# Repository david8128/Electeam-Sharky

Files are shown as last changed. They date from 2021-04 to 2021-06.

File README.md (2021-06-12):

# Electeam-Sharky-ESP32

## OrderMe:
1N4728A: caída de voltaje de 3 a 3.5V - CONFIRMAR
## ORDERED:
This is the firmware for the ESP32-DEVKITV1 microcontroller where throttle, break, LCD screen, motor and more systems are integrated.

Schematic 
<!-- TODO Update schematic here -->
> The PCB Kicad folder is located in (controller_bldc_kicad_Sch_PCB/)[https://github.com/david8128/Electeam-Sharky-ESP32/tree/main/controller_bldc_kicad_Sch_PCB]
## Electrical Specifications for the PCB electronics
<!-- Note the reference of nextion in README, 70mA -->
<!-- TODO Document the current and voltage in Current Sensor -->

<!-- TODO Add the MCU and SMPS specs in README-->
#### Power 
Relay for the Operator Presence Control - aka. Death Man Security System (HAT901 12VDC 20A) = 0.96 W
>MOSFET has been considered for de OPC but the consumtion is higher (Using IRF1010N with a )
For this project is used the MCPWM BLDC motor control (hall sensor feedback) example from ESP-IDF library.

As shown in Schematic there were used two [LM2596 DC-DC HW-411](http://tpelectronic.ir/datasheets/20150123144301750.pdf) converters 

#### Battery
When battery is fully charged the voltage is 40.6V. The BMS open the discharging circuit when the battery voltage is under 32V. 

The energy or maximum energetic storage capacity of the battery is 320Wh.

*This modes will be reviewed under the light of the Shell Echo Marathon Competition.*
## Modes

### Acceleration Optimized

### Soft Start

### Manual

Here you have the documentation of the MCPWM-Hall_Sensor example:

## MCPWM BLDC motor control(hall sensor feedback) Example

This example will show you how to use MCPWM module to control bldc motor with hall sensor feedback
 
The following examples uses MCPWM module to control bldc motor and vary its speed continuously

The bldc motor used for testing this code had hall sensor capture sequence of 6-->4-->5-->1-->3-->2-->6-->4--> and so on

IR2103 3-ph bridge driver is used for testing this example code

User needs to make changes according to the motor and gate driver ic used

## Step 1: Pin assignment
* The gpio init function initializes:
	* GPIO19 is assigned as the MCPWM signal for 1H(UH)
	* GPIO18 is assigned as the MCPWM signal for 1L(UL)
	* GPIO17 is assigned as the MCPWM signal for 2H(VH)
	* GPIO16 is assigned as the MCPWM signal for 2L(VL)
	* GPIO15 is assigned as the MCPWM signal for 3H(WH)
	* GPIO14 is assigned as the MCPWM signal for 3L(WL)
	* GPIO23 is assigned as the MCPWM capture signal for Hall A
	* GPIO25 is assigned as the MCPWM capture signal for HALL B
	* GPIO26 is assigned as the MCPWM capture signal for HALL C

## Step 2: Initialize MCPWM
 * You need to set the frequency and duty cycle of MCPWM timer
 * You need to set the MCPWM channel you want to use, and bind the channel with one of the timers
 * You need to set the capture unit, for POS/NEG edge capture
 * Also reversing the hall sensor BIT weight, will make bldc motor rotate CW or CCW

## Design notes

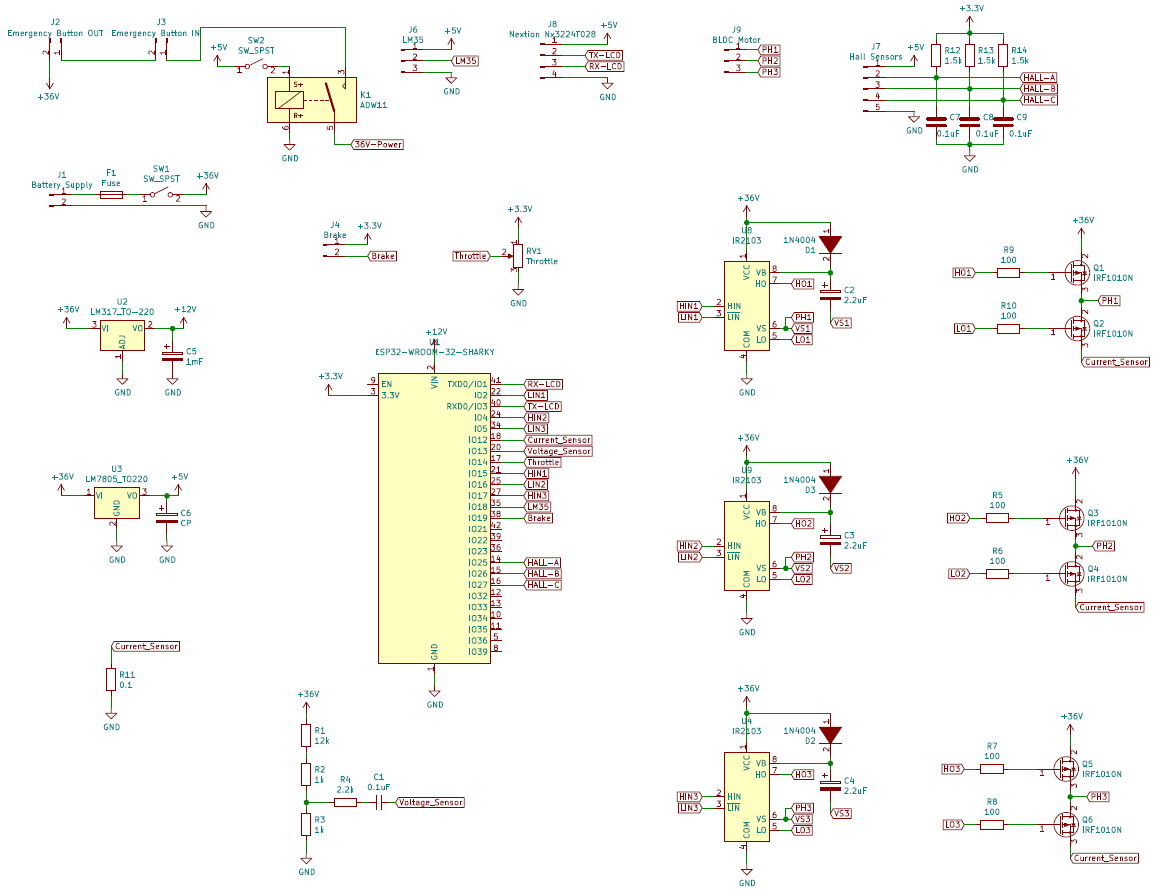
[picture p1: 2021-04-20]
Diseño Electrónico/Esquema y Gerbers PCB/Schematic.png

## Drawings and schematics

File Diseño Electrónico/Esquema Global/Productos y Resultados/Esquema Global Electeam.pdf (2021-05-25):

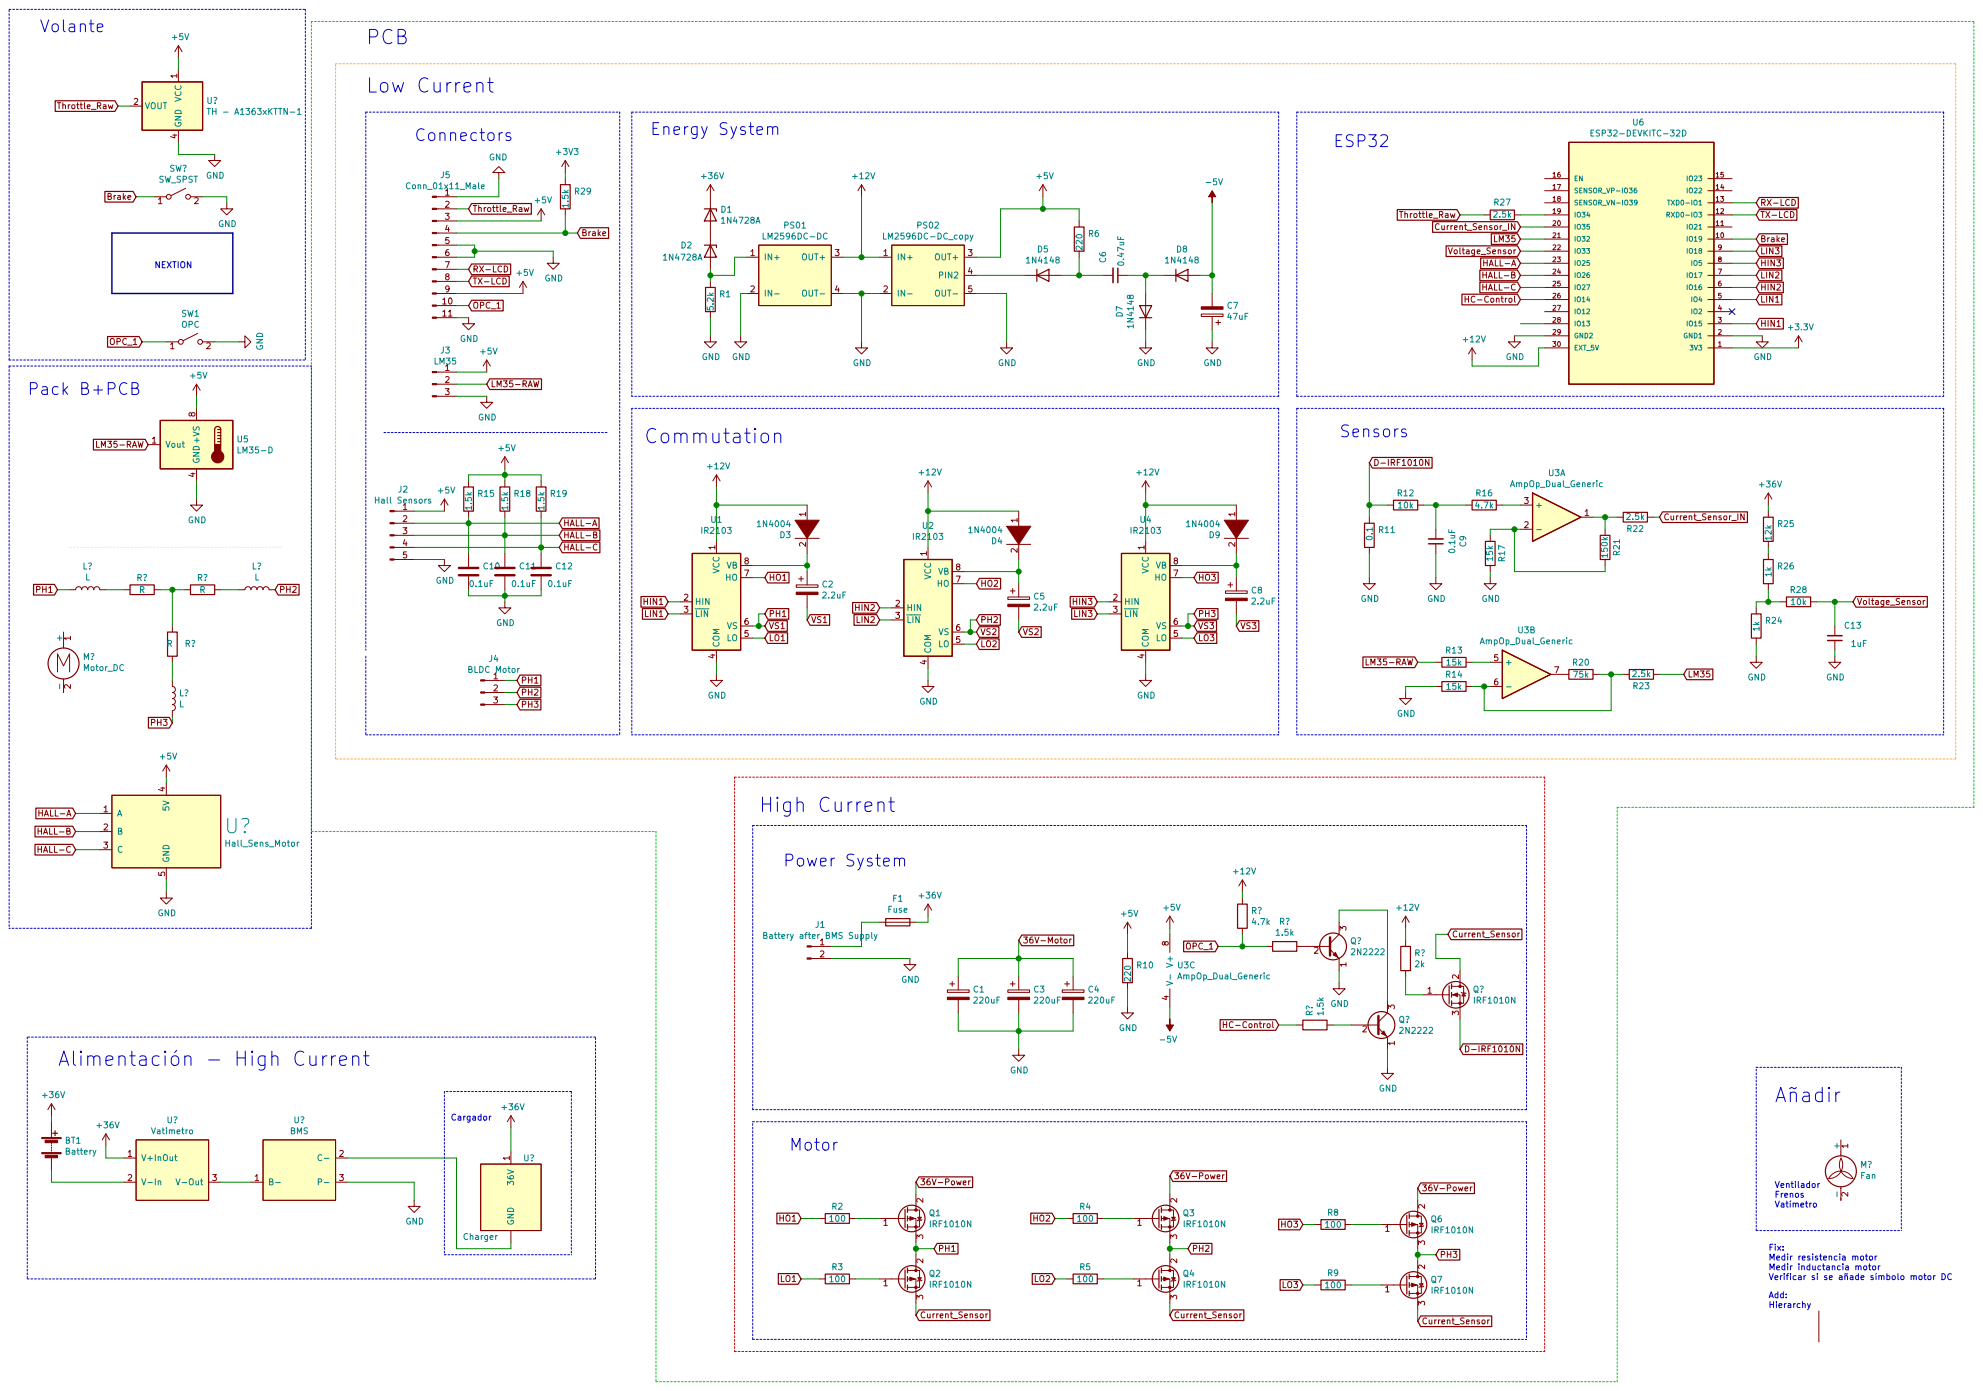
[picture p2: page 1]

Fix: Medir resistencia motor Medir inductancia motor Verificar si se añade símbolo motor DC Commutation

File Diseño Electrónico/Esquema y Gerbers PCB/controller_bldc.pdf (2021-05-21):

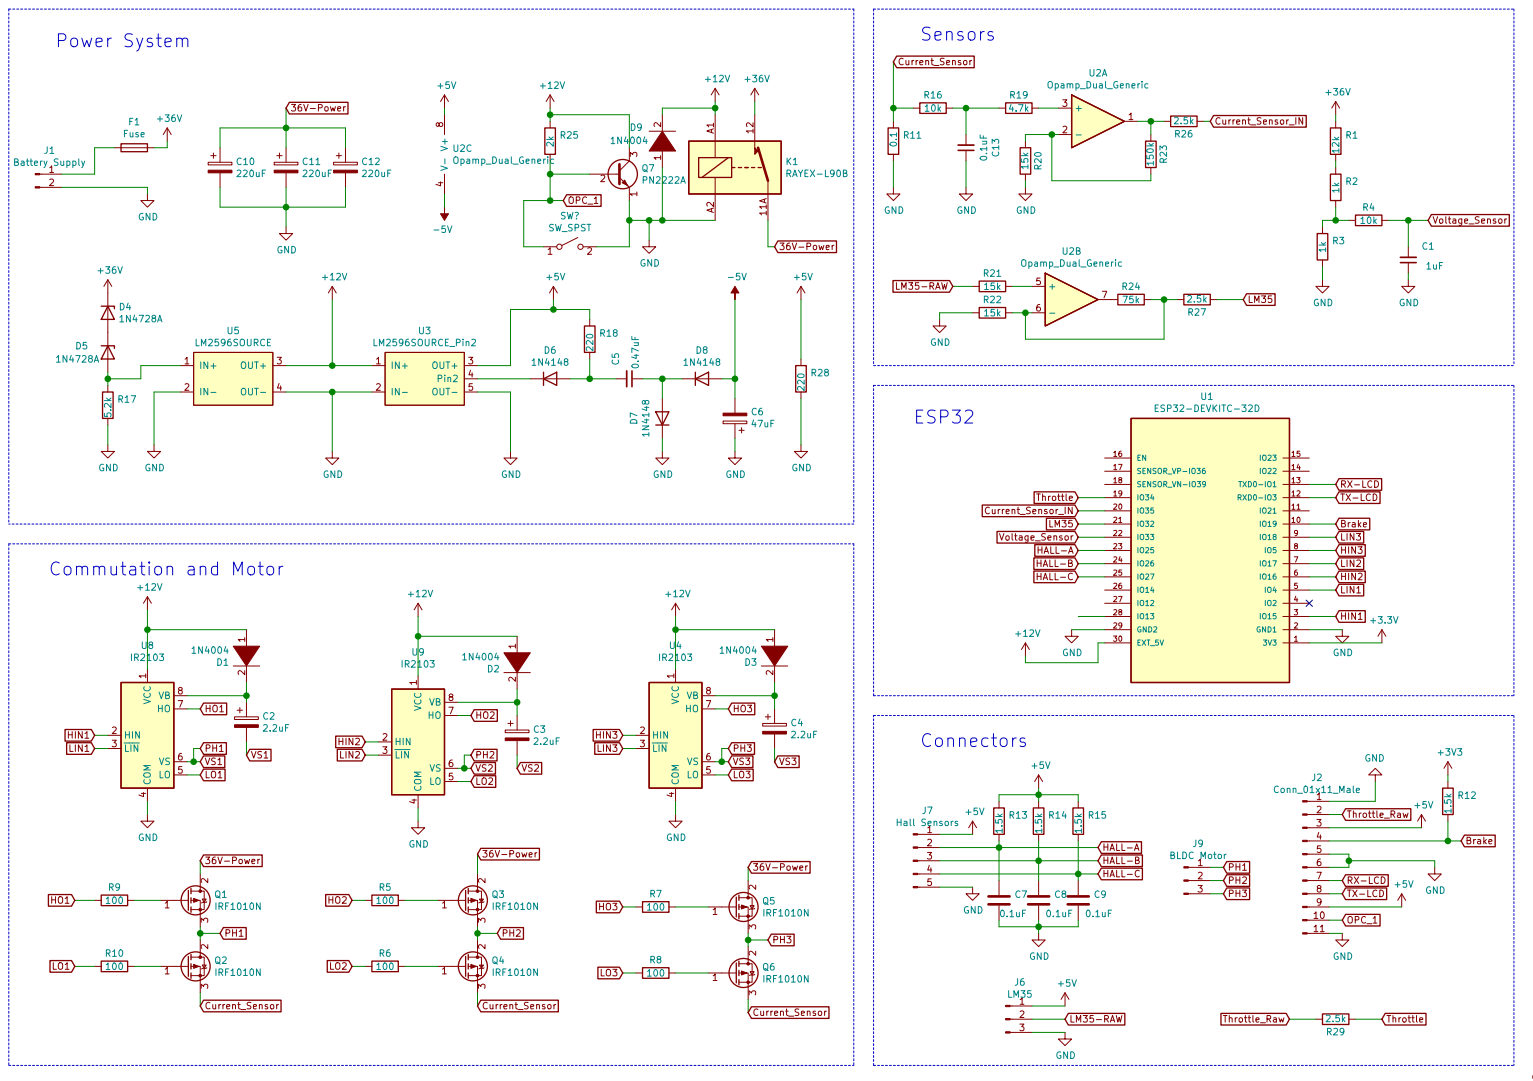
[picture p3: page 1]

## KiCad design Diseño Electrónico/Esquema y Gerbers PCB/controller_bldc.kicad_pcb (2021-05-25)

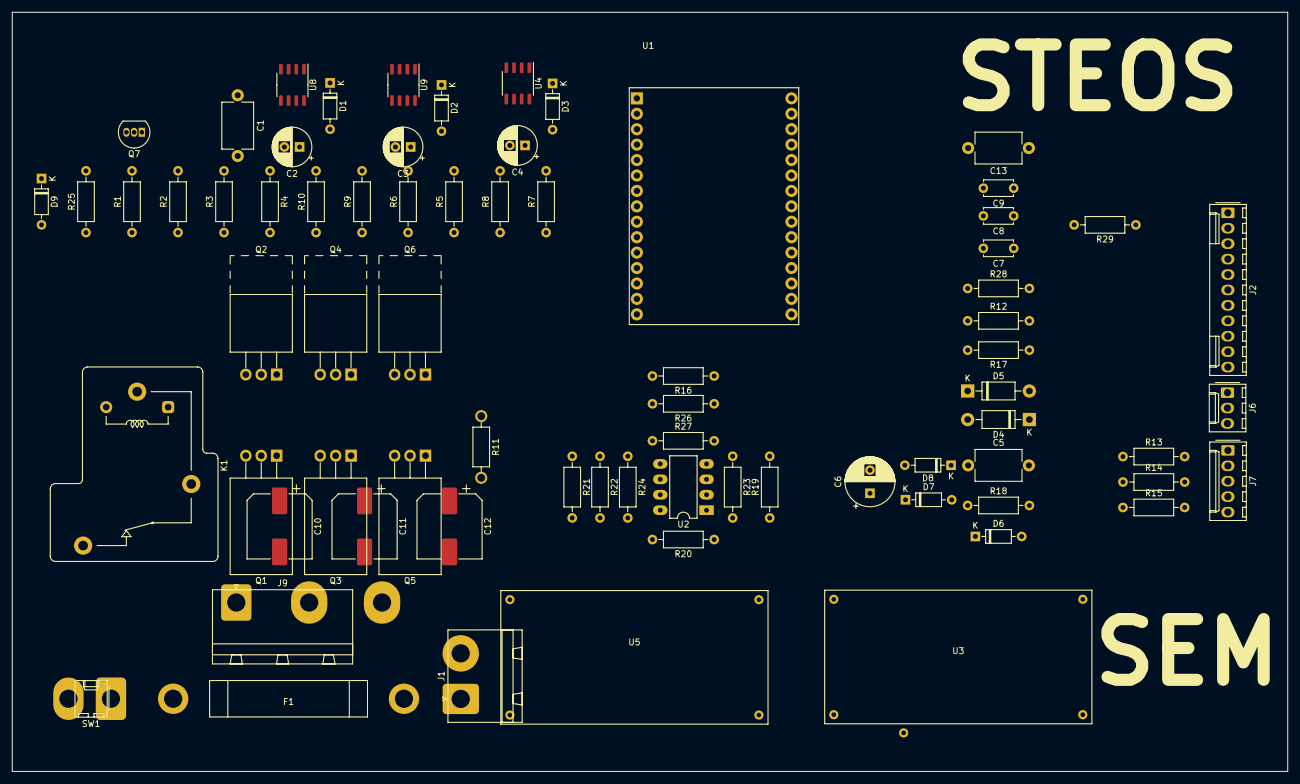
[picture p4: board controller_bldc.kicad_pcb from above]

Board: 2 copper layers, 210.0 x 125.0 mm, 73 parts (0 on the bottom side), 61 nets, no tracks yet.

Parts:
C1: 1uF; C_Disc_D7.5mm_W5.0mm_P10.00mm
C2, C3, C4: 2.2uF; CP_Radial_D6.3mm_P2.50mm
C5: 0.47uF; C_Disc_D7.5mm_W5.0mm_P10.00mm
C6: 47uF; CP_Radial_D8.0mm_P3.80mm
C7, C8, C9: 0.1uF; C_Disc_D4.7mm_W2.5mm_P5.00mm
C10, C11, C12: 220uF; CP_Elec_10x14.3
C13: 0.1uF; C_Disc_D7.5mm_W5.0mm_P10.00mm
D1, D2, D3, D9: 1N4004; D_DO-35_SOD27_P7.62mm_Horizontal
D4, D5: 1N4728A; D_DO-41_SOD81_P10.16mm_Horizontal
D6, D7, D8: 1N4148; D_DO-35_SOD27_P7.62mm_Horizontal
F1: Fuse; Portafusible
J1: Battery Supply; PhoenixContact_GMSTBA_2,5_2-G_1x02_P7.50mm_Horizontal
J2: Conn_01x11_Male; Molex_KK-254_AE-6410-11A_1x11_P2.54mm_Vertical
J6: LM35; Molex_KK-254_AE-6410-03A_1x03_P2.54mm_Vertical
J7: Hall Sensors; Molex_KK-254_AE-6410-05A_1x05_P2.54mm_Vertical
J9: BLDC Motor; PhoenixContact_GMSTBA_2,5_3-G-7,62_1x03_P7.62mm_Horizontal
K1: RAYEX-L90B; Relay_SPST_RAYEX-L90B
Q1, Q3, Q5: IRF1010N; TO-220-3_Horizontal_TabDown
Q2, Q4, Q6: IRF1010N; TO-220-3_Horizontal_TabUp
Q7: PN2222A; TO-92_Inline
R1: 12k; R_Axial_DIN0207_L6.3mm_D2.5mm_P10.16mm_Horizontal
R2, R3: 1k; R_Axial_DIN0207_L6.3mm_D2.5mm_P10.16mm_Horizontal
R4, R16: 10k; R_Axial_DIN0207_L6.3mm_D2.5mm_P10.16mm_Horizontal
R5, R6, R7, R8, R9, R10: 100; R_Axial_DIN0207_L6.3mm_D2.5mm_P10.16mm_Horizontal
R11: 0.1; R_Axial_DIN0207_L6.3mm_D2.5mm_P10.16mm_Horizontal
R12, R13, R14, R15: 1.5k; R_Axial_DIN0207_L6.3mm_D2.5mm_P10.16mm_Horizontal
R17: 5.2k; R_Axial_DIN0207_L6.3mm_D2.5mm_P10.16mm_Horizontal
R18: 220; R_Axial_DIN0207_L6.3mm_D2.5mm_P10.16mm_Horizontal
R19: 4.7k; R_Axial_DIN0207_L6.3mm_D2.5mm_P10.16mm_Horizontal
R20, R21, R22: 15k; R_Axial_DIN0207_L6.3mm_D2.5mm_P10.16mm_Horizontal
R23: 150k; R_Axial_DIN0207_L6.3mm_D2.5mm_P10.16mm_Horizontal
R24: 75k; R_Axial_DIN0207_L6.3mm_D2.5mm_P10.16mm_Horizontal
R25: 2k; R_Axial_DIN0207_L6.3mm_D2.5mm_P10.16mm_Horizontal
R26, R27, R29: 2.5k; R_Axial_DIN0207_L6.3mm_D2.5mm_P10.16mm_Horizontal
R28: 1.2k; R_Axial_DIN0207_L6.3mm_D2.5mm_P10.16mm_Horizontal
SW1: ON_OFF; Molex_KK-254_AE-6410-02A_1x02_P2.54mm_Vertical
U1: ESP32-DEVKITC-32D; MODULE_ESP32-DEVKITC-32D
U2: MC1458P; DIP-8_W7.62mm_LongPads
U3: LM2596SOURCE_Pin2; LM2596DCSourcePin2_Electeam
U4, U8, U9: IR2103; SO-8_3.9x4.9mm_P1.27mm
U5: LM2596SOURCE; LM2596DCSource_Electeam

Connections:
1IN-: R20.1, R23.1, R26.1, U2.2
2IN-: R22.1, R24.1, R27.1, U2.6
36V-Power: C10.1, C11.1, C12.1, K1.11A, K1.11B, Q1.2, Q3.2, Q5.2
+3V3: R12.1, U1.1
+5V: J2.3, J2.9, J6.1, J7.1, R13.1, R14.1, R15.1, R18.1, U2.8, U3.3
+12V: D1.1, D2.1, D3.1, D9.2, K1.A1, Q7.3, R25.1, U1.30, U3.1, U4.1, U5.3, U8.1, U9.1
+36V: D4.1, K1.12, R1.1, SW1.2
-5V: C6.2, D8.2
Brake: J2.4, R12.2, U1.10
Current_Sensor: Q2.3, Q4.3, Q6.3, R11.1, R16.2
Current_Sensor_AO: C13.2, R16.1, R19.2
Current_Sensor_IN: R26.2, U1.19
GND: C1.1, C6.1, C7.2, C8.2, C9.2, C10.2, C11.2, C12.2, C13.1, D7.1, D9.1, J1.2, J2.1, J2.5, J2.6, J2.11, J6.3, J7.5, K1.A2, Q7.1, R3.2, R11.2, R17.2, R20.2, R22.2, R28.2, U1.2, U1.29, U2.4, U3.2, U3.5, U4.4, U5.2, U5.4, U8.4, U9.4
HALL-A: C7.1, J7.2, R13.2, U1.23
HALL-B: C8.1, J7.3, R14.2, U1.24
HALL-C: C9.1, J7.4, R15.2, U1.25
HIN1: U1.3, U8.2
HIN2: U1.6, U9.2
HIN3: U1.8, U4.2
HO1: R9.2, U8.7
HO2: R5.2, U9.7
HO3: R7.2, U4.7
LIN1: U1.5, U8.3
LIN2: U1.7, U9.3
LIN3: U1.9, U4.3
LM35: R27.2, U1.18
LM35-RAW: J6.2, R21.2
LO1: R10.2, U8.5
LO2: R6.2, U9.5
LO3: R8.2, U4.5
unnamed: C2.1, D1.2, U8.8
unnamed: C3.1, D2.2, U9.8
unnamed: C4.1, D3.2, U4.8
unnamed: C5.1, D7.2, D8.1
unnamed: C5.2, D6.2, R18.2
unnamed: D4.2, D5.1
unnamed: D5.2, R17.1, U5.1
unnamed: D6.1, U3.4
unnamed: F1.1, SW1.1
unnamed: F1.2, J1.1
unnamed: Q1.1, R9.1
unnamed: Q2.1, R10.1
unnamed: Q3.1, R5.1
unnamed: Q4.1, R6.1
unnamed: Q5.1, R7.1
unnamed: Q6.1, R8.1
unnamed: R1.2, R2.1
unnamed: R2.2, R3.1, R4.2
unnamed: R19.1, U2.3
unnamed: R21.1, U2.5
unnamed: R23.2, U2.1
unnamed: R24.2, U2.7
OPC_1: J2.10, Q7.2, R25.2
PH1: C2.2, J9.1, Q1.3, Q2.2, U8.6
PH2: C3.2, J9.2, Q3.3, Q4.2, U9.6
PH3: C4.2, J9.3, Q5.3, Q6.2, U4.6
RX-LCD: J2.7, U1.13
TX-LCD: J2.8, U1.12
Throttle: R28.1, R29.2, U1.20
Throttle_Raw: J2.2, R29.1
Voltage_Sensor: C1.2, R4.1, U1.28

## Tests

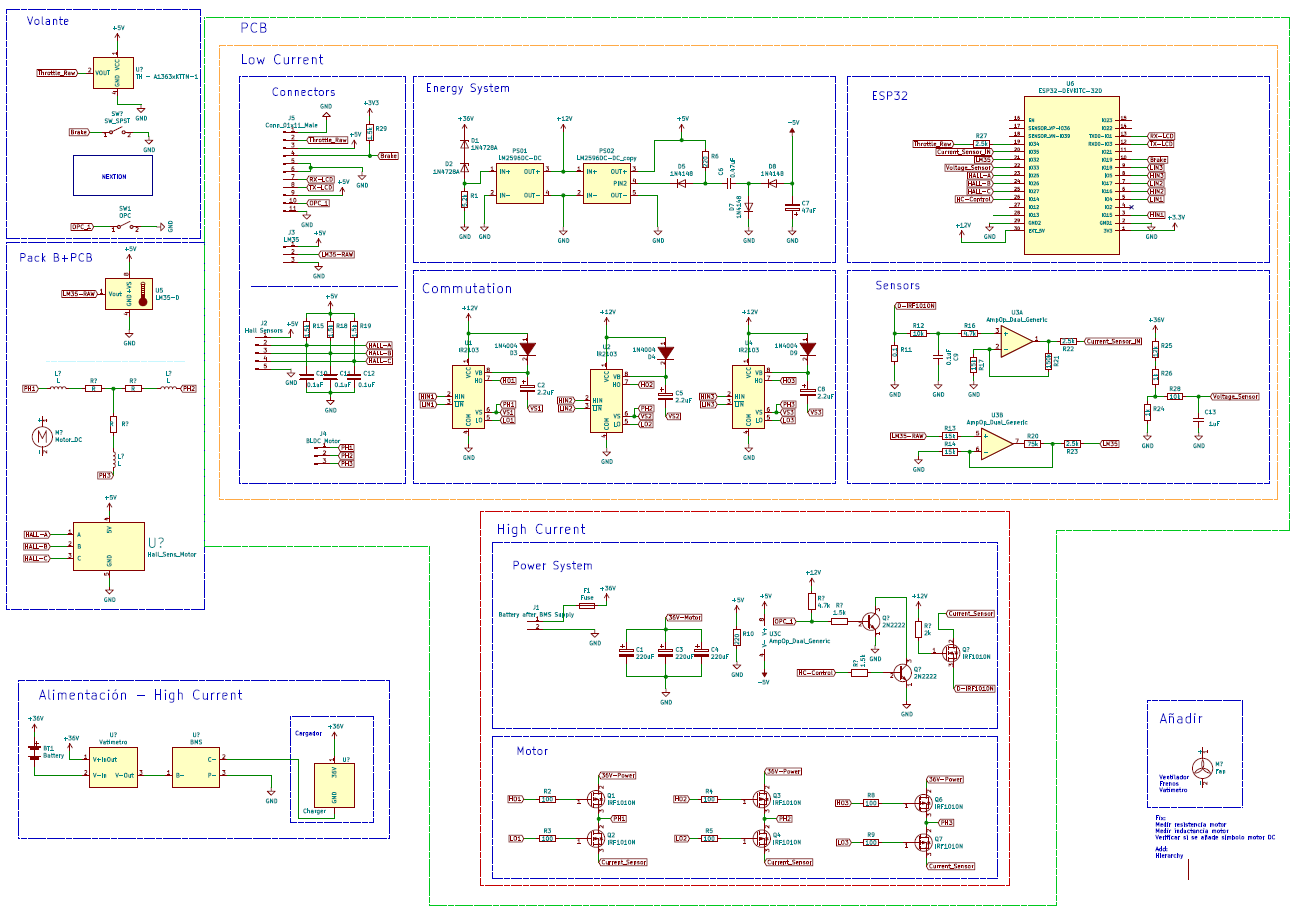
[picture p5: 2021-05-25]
Diseño Electrónico/Esquema Global/Productos y Resultados/Esquema v2.1.png

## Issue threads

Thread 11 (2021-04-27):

Check and fix threshold to start accelerating

david8128, 2021-04-27:
Take into account the line 293 inside [sharky.c](https://github.com/david8128/Electeam-Sharky-ESP32/blob/main/main/sharky.c)

Closed 2021-04-30.

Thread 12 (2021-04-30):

Fix overvoltage issue in sensors

david8128, 2021-04-30:

Closed 2021-04-30.

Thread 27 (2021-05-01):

Send from ESP32 and recieve in the Nextion Screen

david8128, 2021-05-01:

david8128, 2021-05-02:
Created a new blank project in Nextion Editor with only a text component, and within the uart_async_rxtxtasks_main.c tried to send refresh commands to page and text component. It doesn't works.

Trying with ESP32_Weather_Station, foud that works perfectly with the `HardwareSerial Serial1(0);`

Closed 2021-05-10.

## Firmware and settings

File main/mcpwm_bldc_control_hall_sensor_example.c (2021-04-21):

/* MCPWM basic config example

   This example code is in the Public Domain (or CC0 licensed, at your option.)

   Unless required by applicable law or agreed to in writing, this
   software is distributed on an "AS IS" BASIS, WITHOUT WARRANTIES OR
   CONDITIONS OF ANY KIND, either express or implied.
*/

/*
 * This example will show you how to use each submodule of MCPWM unit.
 * The example can't be used without modifying the code first.
 * Edit the macros at the top of mcpwm_example_basic_config.c to enable/disable the submodules which are used in the example.
 */

// Include FreeRTOS for both MCPWM and ADC
#include "freertos/FreeRTOS.h"
#include "freertos/task.h"

// Include for MCPWM
#include <stdio.h>
#include "string.h"
#include "freertos/queue.h"
#include "esp_attr.h"
#include "soc/rtc.h"
#include "driver/mcpwm.h"
#include "soc/mcpwm_periph.h"

// Include for ADC
#include <stdlib.h>
#include "driver/gpio.h"
#include "driver/adc.h"
#include "esp_adc_cal.h"

// Define for ADC
#define DEFAULT_VREF    1100        //Use adc2_vref_to_gpio() to obtain a better estimate
#define NO_OF_SAMPLES   64          //Multisampling


static esp_adc_cal_characteristics_t *adc_chars;
#if CONFIG_IDF_TARGET_ESP32
static const adc_channel_t channel = ADC_CHANNEL_6;     //GPIO34 if ADC1, GPIO14 if ADC2
static const adc_bits_width_t width = ADC_WIDTH_BIT_12;
#elif CONFIG_IDF_TARGET_ESP32S2
static const adc_channel_t channel = ADC_CHANNEL_6;     // GPIO7 if ADC1, GPIO17 if ADC2
static const adc_bits_width_t width = ADC_WIDTH_BIT_13;
#endif
static const adc_atten_t atten = ADC_ATTEN_DB_11;
static const adc_unit_t unit = ADC_UNIT_1;

//Define for MCPWM

#define INITIAL_DUTY 10.0   //initial duty cycle is 10.0%
#define MCPWM_GPIO_INIT 0   //select which function to use to initialize gpio signals

#define GPIO_HALL_TEST_SIGNAL 0     //Make this 1 to enable generation of hall sensors test signal on GPIO13, 12, 14
#define CHANGE_DUTY_CONTINUOUSLY 0  //Make this 1 to change duty continuously

#define CAP_SIG_NUM 3   //three capture signals from HALL-A, HALL-B, HALL-C
#define CAP0_INT_EN BIT(27)  //Capture 0 interrupt bit
#define CAP1_INT_EN BIT(28)  //Capture 1 interrupt bit
#define CAP2_INT_EN BIT(29)  //Capture 2 interrupt bit

#define GPIO_PWM0A_OUT 15   //Set GPIO 19 as PWM0A
#define GPIO_PWM0B_OUT 04   //Set GPIO 18 as PWM0B
#define GPIO_PWM1A_OUT 16   //Set GPIO 17 as PWM1A
#define GPIO_PWM1B_OUT 17   //Set GPIO 16 as PWM1B
#define GPIO_PWM2A_OUT 05   //Set GPIO 15 as PWM2A
#define GPIO_PWM2B_OUT 18   //Set GPIO 14 as PWM2B
#define GPIO_CAP0_IN   23   //Set GPIO 23 as  CAP0
#define GPIO_CAP1_IN   25   //Set GPIO 25 as  CAP1
#define GPIO_CAP2_IN   26   //Set GPIO 26 as  CAP2

#define GPIO_BREAK  19   //Set GPIO 26 as  CAP2


typedef struct {
    uint32_t capture_signal;
    mcpwm_capture_signal_t sel_cap_signal;
} capture;

static uint32_t hall_sensor_value = 0;
static uint32_t hall_sensor_previous = 0;

xQueueHandle cap_queue;
xQueueHandle cap_queue2;

static mcpwm_dev_t *MCPWM[2] = {&MCPWM0, &MCPWM1};


// Functions MCPWM
static void mcpwm_example_gpio_initialize(void)
{
    printf("initializing mcpwm bldc control gpio...\n");
#if MCPWM_GPIO_INIT
    mcpwm_gpio_init(MCPWM_UNIT_0, MCPWM0A, GPIO_PWM0A_OUT);
    mcpwm_gpio_init(MCPWM_UNIT_0, MCPWM0B, GPIO_PWM0B_OUT);
    mcpwm_gpio_init(MCPWM_UNIT_0, MCPWM1A, GPIO_PWM1A_OUT);
    mcpwm_gpio_init(MCPWM_UNIT_0, MCPWM1B, GPIO_PWM1B_OUT);
    mcpwm_gpio_init(MCPWM_UNIT_0, MCPWM2A, GPIO_PWM2A_OUT);
    mcpwm_gpio_init(MCPWM_UNIT_0, MCPWM2B, GPIO_PWM2B_OUT);
    mcpwm_gpio_init(MCPWM_UNIT_0, MCPWM_CAP_0, GPIO_CAP0_IN);
    mcpwm_gpio_init(MCPWM_UNIT_0, MCPWM_CAP_1, GPIO_CAP1_IN);
    mcpwm_gpio_init(MCPWM_UNIT_0, MCPWM_CAP_2, GPIO_CAP2_IN);
#else
    mcpwm_pin_config_t pin_config = {
        .mcpwm0a_out_num = GPIO_PWM0A_OUT,
        .mcpwm0b_out_num = GPIO_PWM0B_OUT,
        .mcpwm1a_out_num = GPIO_PWM1A_OUT,
        .mcpwm1b_out_num = GPIO_PWM1B_OUT,
        .mcpwm2a_out_num = GPIO_PWM2A_OUT,
        .mcpwm2b_out_num = GPIO_PWM2B_OUT,
        .mcpwm_cap0_in_num   = GPIO_CAP0_IN,
        .mcpwm_cap1_in_num   = GPIO_CAP1_IN,
        .mcpwm_cap2_in_num   = GPIO_CAP2_IN,
        .mcpwm_sync0_in_num  = -1,  //Not used
        .mcpwm_sync1_in_num  = -1,  //Not used
        .mcpwm_sync2_in_num  = -1,  //Not used
        .mcpwm_fault0_in_num = -1,  //Not used
        .mcpwm_fault1_in_num = -1,  //Not used
        .mcpwm_fault2_in_num = -1   //Not used
    };
    mcpwm_set_pin(MCPWM_UNIT_0, &pin_config);
#endif
    gpio_pulldown_en(GPIO_CAP0_IN);    //Enable pull down on CAP0   signal
    gpio_pulldown_en(GPIO_CAP1_IN);    //Enable pull down on CAP1   signal
    gpio_pulldown_en(GPIO_CAP2_IN);    //Enable pull down on CAP2   signal
}

#if GPIO_HALL_TEST_SIGNAL
/**
 * @brief Set gpio 13, 12, 14  as our test signal of hall sensors, that generates high-low waveform continuously
 *        Attach this pins to GPIO 27, 26, 25 respectively for capture unit
 */
static void gpio_test_signal(void *arg)
{
    printf("intializing test signal...\n");
    gpio_config_t gp;
    gp.intr_type = GPIO_INTR_DISABLE;
    gp.mode = GPIO_MODE_OUTPUT;
    gp.pin_bit_mask = GPIO_SEL_13 | GPIO_SEL_12 | GPIO_SEL_14;
    gpio_config(&gp);
    while (1) {
        gpio_set_level(GPIO_NUM_13, 1); //Set H1 high
        gpio_set_level(GPIO_NUM_12, 0); //Set H2 low
        gpio_set_level(GPIO_NUM_14, 1); //Set H3 high
        vTaskDelay(1);
        gpio_set_level(GPIO_NUM_14, 0); //Set H3 low
        vTaskDelay(1);
        gpio_set_level(GPIO_NUM_12, 1); //Set H2 high
        vTaskDelay(1);
        gpio_set_level(GPIO_NUM_13, 0); //Set H1 low
        vTaskDelay(1);
        gpio_set_level(GPIO_NUM_14, 1); //Set H3 high
        vTaskDelay(1);
        gpio_set_level(GPIO_NUM_12, 0); //Set H2 high
        vTaskDelay(1);
    }
}
#endif

/**
 * @brief When interrupt occurs, we receive the counter value and display the time between two rising edge
 */
static void disp_captured_signal(void *arg)
{
    uint32_t *current_cap_value = (uint32_t *)malloc(sizeof(CAP_SIG_NUM));
    uint32_t *previous_cap_value = (uint32_t *)malloc(sizeof(CAP_SIG_NUM));
    capture evt;
    while (1) {
        xQueueReceive(cap_queue, &evt, portMAX_DELAY);
        if (evt.sel_cap_signal == MCPWM_SELECT_CAP0) {
            current_cap_value[0] = evt.capture_signal - previous_cap_value[0];
            previous_cap_value[0] = evt.capture_signal;
            current_cap_value[0] = (current_cap_value[0] / 10000) * (10000000000 / rtc_clk_apb_freq_get());
            //printf("CAP0 : %d us\n", current_cap_value[0]);
        }
        if (evt.sel_cap_signal == MCPWM_SELECT_CAP1) {
            current_cap_value[1] = evt.capture_signal - previous_cap_value[1];
            previous_cap_value[1] = evt.capture_signal;
            current_cap_value[1] = (current_cap_value[1] / 10000) * (10000000000 / rtc_clk_apb_freq_get());
            //printf("CAP1 : %d us\n", current_cap_value[1]);
        }
        if (evt.sel_cap_signal == MCPWM_SELECT_CAP2) {
            current_cap_value[2] = evt.capture_signal -  previous_cap_value[2];
            previous_cap_value[2] = evt.capture_signal;
            current_cap_value[2] = (current_cap_value[2] / 10000) * (10000000000 / rtc_clk_apb_freq_get());
            //printf("CAP2 : %d us\n", current_cap_value[2]);
        }
    }
}

/**
 * @brief this is ISR handler function, here we check for interrupt that triggers rising edge on CAP0 signal and according take action
 */
static void IRAM_ATTR isr_handler(void *arg)
{
    uint32_t mcpwm_intr_status;
    capture evt;
    mcpwm_intr_status = MCPWM[MCPWM_UNIT_0]->int_st.val; //Read interrupt status
    if (mcpwm_intr_status & CAP0_INT_EN) { //Check for interrupt on rising edge on CAP0 signal
        evt.capture_signal = mcpwm_capture_signal_get_value(MCPWM_UNIT_0, MCPWM_SELECT_CAP0); //get capture signal counter value
        evt.sel_cap_signal = MCPWM_SELECT_CAP0;
        xQueueSendFromISR(cap_queue, &evt, NULL);
    }
    if (mcpwm_intr_status & CAP1_INT_EN) { //Check for interrupt on rising edge on CAP1 signal
        evt.capture_signal = mcpwm_capture_signal_get_value(MCPWM_UNIT_0, MCPWM_SELECT_CAP1); //get capture signal counter value
        evt.sel_cap_signal = MCPWM_SELECT_CAP1;
        xQueueSendFromISR(cap_queue, &evt, NULL);
    }
    if (mcpwm_intr_status & CAP2_INT_EN) { //Check for interrupt on rising edge on CAP2 signal
        evt.capture_signal = mcpwm_capture_signal_get_value(MCPWM_UNIT_0, MCPWM_SELECT_CAP2); //get capture signal counter value
        evt.sel_cap_signal = MCPWM_SELECT_CAP2;
        xQueueSendFromISR(cap_queue, &evt, NULL);
    }
    MCPWM[MCPWM_UNIT_0]->int_clr.val = mcpwm_intr_status;
}

#if CHANGE_DUTY_CONTINUOUSLY
static void change_duty(void *arg)
{
    int j;
    while (1) {
        for (j = 0; j < 18; j++) {
            //printf("duty cycle: %d\n", (0 +j*50));
            mcpwm_set_duty(MCPWM_UNIT_0, MCPWM_TIMER_0, MCPWM_OPR_A, (INITIAL_DUTY + j * 5.0));
            mcpwm_set_duty(MCPWM_UNIT_0, MCPWM_TIMER_0, MCPWM_OPR_B, (INITIAL_DUTY + j * 5.0));
            mcpwm_set_duty(MCPWM_UNIT_0, MCPWM_TIMER_1, MCPWM_OPR_A, (INITIAL_DUTY + j * 5.0));
            mcpwm_set_duty(MCPWM_UNIT_0, MCPWM_TIMER_1, MCPWM_OPR_B, (INITIAL_DUTY + j * 5.0));
            mcpwm_set_duty(MCPWM_UNIT_0, MCPWM_TIMER_2, MCPWM_OPR_A, (INITIAL_DUTY + j * 5.0));
            mcpwm_set_duty(MCPWM_UNIT_0, MCPWM_TIMER_2, MCPWM_OPR_B, (INITIAL_DUTY + j * 5.0));
            vTaskDelay(500 / portTICK_RATE_MS);
        }
    }
}
#endif

/**
 * @brief Configure whole MCPWM module for bldc motor control
 */
static void mcpwm_example_bldc_control(void *arg)
{
    
    //1. mcpwm gpio initialization
    mcpwm_example_gpio_initialize();

    //2. initial mcpwm configuration
    printf("Configuring Initial Parameters of mcpwm bldc control...\n");
    mcpwm_config_t pwm_config;
    pwm_config.frequency = 1000;    //frequency = 1000Hz
    pwm_config.cmpr_a = 50.0;    //duty cycle of PWMxA = 50.0%
    pwm_config.cmpr_b = 0;    //duty cycle of PWMxb = 50.0%
    pwm_config.counter_mode = MCPWM_UP_COUNTER;
    pwm_config.duty_mode = MCPWM_DUTY_MODE_1;
    mcpwm_init(MCPWM_UNIT_0, MCPWM_TIMER_0, &pwm_config);    //Configure PWM0A & PWM0B with above settings
    mcpwm_init(MCPWM_UNIT_0, MCPWM_TIMER_1, &pwm_config);    //Configure PWM1A & PWM1B with above settings
    mcpwm_init(MCPWM_UNIT_0, MCPWM_TIMER_2, &pwm_config);    //Configure PWM2A & PWM2B with above settings
    //3. Capture configuration
    //configure CAP0, CAP1 and CAP2 signal to start capture counter on rising edge
    //we generate a gpio_test_signal of 20ms on GPIO 12 and connect it to one of the capture signal, the disp_captured_function displays the time between rising edge
    //In general practice you can connect Capture  to external signal, measure time between rising edge or falling edge and take action accordingly
    mcpwm_capture_enable(MCPWM_UNIT_0, MCPWM_SELECT_CAP0, MCPWM_POS_EDGE, 0);  //capture signal on rising edge, pulse num = 0 i.e. 800,000,000 counts is equal to one second
    mcpwm_capture_enable(MCPWM_UNIT_0, MCPWM_SELECT_CAP1, MCPWM_POS_EDGE, 0);  //capture signal on rising edge, pulse num = 0 i.e. 800,000,000 counts is equal to one second
    mcpwm_capture_enable(MCPWM_UNIT_0, MCPWM_SELECT_CAP2, MCPWM_POS_EDGE, 0);  //capture signal on rising edge, pulse num = 0 i.e. 800,000,000 counts is equal to one second
    //enable interrupt, so each this a rising edge occurs interrupt is triggered
    MCPWM[MCPWM_UNIT_0]->int_ena.val = (CAP0_INT_EN | CAP1_INT_EN | CAP2_INT_EN);  //Enable interrupt on  CAP0, CAP1 and CAP2 signal
    mcpwm_isr_register(MCPWM_UNIT_0, isr_handler, NULL, ESP_INTR_FLAG_IRAM, NULL);  //Set ISR Handler
    
    //According to the hall sensor input value take action on PWM0A/0B/1A/1B/2A/2B
    uint32_t adc_reading_MCPWM = 0;
    float duty_cycle = 0.0;
    while (1) {
        xQueueReceive(cap_queue2, &adc_reading_MCPWM, portMAX_DELAY);
        hall_sensor_value = (gpio_get_level(GPIO_CAP2_IN) * 1) + (gpio_get_level(GPIO_CAP1_IN) * 2) + (gpio_get_level(GPIO_CAP0_IN) * 4);
        if(gpio_get_level(GPIO_BREAK) == 1){
            printf("hall_sen val: %d\n", hall_sensor_value);
            mcpwm_config_t pwm_config;
            pwm_config.frequency = 1000;    //frequency = 1000Hz
            duty_cycle = (adc_reading_MCPWM-950.0)/31.45;
            if( duty_cycle < 0.0 ){
                duty_cycle = 0.0;    
            }else{
                duty_cycle = (adc_reading_MCPWM-950)/31.45;
            }
            printf("duty_cycle: %f\n", duty_cycle);
            pwm_config.cmpr_a = duty_cycle;
            pwm_config.cmpr_b = 0;    
            pwm_config.counter_mode = MCPWM_UP_COUNTER;
            if (hall_sensor_value == 2) {
                printf("Condicion: %d\n", hall_sensor_value);
                mcpwm_set_signal_low(MCPWM_UNIT_0, MCPWM_TIMER_2, MCPWM_OPR_A);
                mcpwm_set_signal_low(MCPWM_UNIT_0, MCPWM_TIMER_2, MCPWM_OPR_B);
                mcpwm_set_signal_low(MCPWM_UNIT_0, MCPWM_TIMER_1, MCPWM_OPR_A);
                mcpwm_set_signal_high(MCPWM_UNIT_0, MCPWM_TIMER_1, MCPWM_OPR_B);
                //MCPWMXA to duty mode 1 and MCPWMXB to duty mode 0 or vice versa will generate MCPWM compliment signal of each other, there are also other ways to do it
                
                mcpwm_init(MCPWM_UNIT_0, MCPWM_TIMER_0, &pwm_config);    //Configure PWM0A & PWM0B with above settings
                mcpwm_set_duty_type(MCPWM_UNIT_0, MCPWM_TIMER_0, MCPWM_OPR_A, MCPWM_DUTY_MODE_0); //Set PWM0A to duty mode one
                mcpwm_set_duty_type(MCPWM_UNIT_0, MCPWM_TIMER_0, MCPWM_OPR_B, MCPWM_DUTY_MODE_0); //Set PWM0B back to duty mode zero
                mcpwm_deadtime_enable(MCPWM_UNIT_0, MCPWM_TIMER_0, MCPWM_BYPASS_FED, 100, 100);   //Deadtime of 10us
            }
            if (hall_sensor_value == 6) {
                printf("Condicion: %d\n", hall_sensor_value);
                mcpwm_set_signal_low(MCPWM_UNIT_0, MCPWM_TIMER_0, MCPWM_OPR_A);
                mcpwm_set_signal_low(MCPWM_UNIT_0, MCPWM_TIMER_0, MCPWM_OPR_B);
                mcpwm_deadtime_disable(MCPWM_UNIT_0, MCPWM_TIMER_0);
                mcpwm_set_signal_low(MCPWM_UNIT_0, MCPWM_TIMER_1, MCPWM_OPR_A);
                mcpwm_set_signal_high(MCPWM_UNIT_0, MCPWM_TIMER_1, MCPWM_OPR_B);
                //MCPWMXA to duty mode 1 and MCPWMXB to duty mode 0 or vice versa will generate MCPWM compliment signal of each other, there are also other ways to do it
                mcpwm_init(MCPWM_UNIT_0, MCPWM_TIMER_2, &pwm_config);    //Configure PWM0A & PWM0B with above settings
                mcpwm_set_duty_type(MCPWM_UNIT_0, MCPWM_TIMER_2, MCPWM_OPR_A, MCPWM_DUTY_MODE_0); //Set PWM2A to duty mode one
                mcpwm_set_duty_type(MCPWM_UNIT_0, MCPWM_TIMER_2, MCPWM_OPR_B, MCPWM_DUTY_MODE_0); //Set PWM2B back to duty mode zero
                mcpwm_deadtime_enable(MCPWM_UNIT_0, MCPWM_TIMER_2, MCPWM_BYPASS_FED, 100, 100);   //Deadtime of 10us
            }
            if (hall_sensor_value == 4) {
                printf("Condicion: %d\n", hall_sensor_value);
                mcpwm_set_signal_low(MCPWM_UNIT_0, MCPWM_TIMER_1, MCPWM_OPR_A);
                mcpwm_set_signal_low(MCPWM_UNIT_0, MCPWM_TIMER_1, MCPWM_OPR_B);
                mcpwm_set_signal_low(MCPWM_UNIT_0, MCPWM_TIMER_0, MCPWM_OPR_A);
                mcpwm_set_signal_high(MCPWM_UNIT_0, MCPWM_TIMER_0, MCPWM_OPR_B);
                //MCPWMXA to duty mode 1 and MCPWMXB to duty mode 0 or vice versa will generate MCPWM compliment signal of each other, there are also other ways to do it
                mcpwm_init(MCPWM_UNIT_0, MCPWM_TIMER_2, &pwm_config);    //Configure PWM0A & PWM0B with above settings
                mcpwm_set_duty_type(MCPWM_UNIT_0, MCPWM_TIMER_2, MCPWM_OPR_A, MCPWM_DUTY_MODE_0); //Set PWM2A to duty mode one
                mcpwm_set_duty_type(MCPWM_UNIT_0, MCPWM_TIMER_2, MCPWM_OPR_B, MCPWM_DUTY_MODE_0); //Set PWM2B back to duty mode zero
                mcpwm_deadtime_enable(MCPWM_UNIT_0, MCPWM_TIMER_2, MCPWM_BYPASS_FED, 100, 100);   //Deadtime of 10us
            }
            if (hall_sensor_value == 5) {
                printf("Condicion: %d\n", hall_sensor_value);
                mcpwm_set_signal_low(MCPWM_UNIT_0, MCPWM_TIMER_2, MCPWM_OPR_A);
                mcpwm_set_signal_low(MCPWM_UNIT_0, MCPWM_TIMER_2, MCPWM_OPR_B);
                mcpwm_deadtime_disable(MCPWM_UNIT_0, MCPWM_TIMER_2);
                mcpwm_set_signal_low(MCPWM_UNIT_0, MCPWM_TIMER_0, MCPWM_OPR_A);
                mcpwm_set_signal_high(MCPWM_UNIT_0, MCPWM_TIMER_0, MCPWM_OPR_B);
                //MCPWMXA to duty mode 1 and MCPWMXB to duty mode 0 or vice versa will generate MCPWM compliment signal of each other, there are also other ways to do it
                mcpwm_init(MCPWM_UNIT_0, MCPWM_TIMER_1, &pwm_config);    //Configure PWM0A & PWM0B with above settings
                mcpwm_set_duty_type(MCPWM_UNIT_0, MCPWM_TIMER_1, MCPWM_OPR_A, MCPWM_DUTY_MODE_0); //Set PWM1A to duty mode one
                mcpwm_set_duty_type(MCPWM_UNIT_0, MCPWM_TIMER_1, MCPWM_OPR_B, MCPWM_DUTY_MODE_0); //Set PWM1B back to duty mode zero
                mcpwm_deadtime_enable(MCPWM_UNIT_0, MCPWM_TIMER_1, MCPWM_BYPASS_FED, 100, 100);   //Deadtime of 10uss
            }
            if (hall_sensor_value == 1) {
                printf("Condicion: %d\n", hall_sensor_value);
                mcpwm_set_signal_low(MCPWM_UNIT_0, MCPWM_TIMER_0, MCPWM_OPR_A);
                mcpwm_set_signal_low(MCPWM_UNIT_0, MCPWM_TIMER_0, MCPWM_OPR_B);
                mcpwm_set_signal_low(MCPWM_UNIT_0, MCPWM_TIMER_2, MCPWM_OPR_A);
                mcpwm_set_signal_high(MCPWM_UNIT_0, MCPWM_TIMER_2, MCPWM_OPR_B);
                //MCPWMXA to duty mode 1 and MCPWMXB to duty mode 0 or vice versa will generate MCPWM compliment signal of each other, there are also other ways to do it
                mcpwm_init(MCPWM_UNIT_0, MCPWM_TIMER_1, &pwm_config);    //Configure PWM0A & PWM0B with above settings
                mcpwm_set_duty_type(MCPWM_UNIT_0, MCPWM_TIMER_1, MCPWM_OPR_A, MCPWM_DUTY_MODE_0); //Set PWM1A to duty mode one
                mcpwm_set_duty_type(MCPWM_UNIT_0, MCPWM_TIMER_1, MCPWM_OPR_B, MCPWM_DUTY_MODE_0); //Set PWM1B back to duty mode zero
                mcpwm_deadtime_enable(MCPWM_UNIT_0, MCPWM_TIMER_1, MCPWM_BYPASS_FED, 100, 100);   //Deadtime of 10uss
            }
            if (hall_sensor_value == 3) {
                printf("Condicion: %d\n", hall_sensor_value);
                mcpwm_set_signal_low(MCPWM_UNIT_0, MCPWM_TIMER_1, MCPWM_OPR_A);
                mcpwm_set_signal_low(MCPWM_UNIT_0, MCPWM_TIMER_1, MCPWM_OPR_B);
                mcpwm_deadtime_disable(MCPWM_UNIT_0, MCPWM_TIMER_1);
                mcpwm_set_signal_low(MCPWM_UNIT_0, MCPWM_TIMER_2, MCPWM_OPR_A);
                mcpwm_set_signal_high(MCPWM_UNIT_0, MCPWM_TIMER_2, MCPWM_OPR_B);
                //MCPWMXA to duty mode 1 and MCPWMXB to duty mode 0 or vice versa will generate MCPWM compliment signal of each other, there are also other ways to do it
                mcpwm_init(MCPWM_UNIT_0, MCPWM_TIMER_0, &pwm_config);    //Configure PWM0A & PWM0B with above settings
                mcpwm_set_duty_type(MCPWM_UNIT_0, MCPWM_TIMER_0, MCPWM_OPR_A, MCPWM_DUTY_MODE_0); //Set PWM0A to duty mode one
                mcpwm_set_duty_type(MCPWM_UNIT_0, MCPWM_TIMER_0, MCPWM_OPR_B, MCPWM_DUTY_MODE_0); //Set PWM0B back to duty mode zero
                mcpwm_deadtime_enable(MCPWM_UNIT_0, MCPWM_TIMER_0, MCPWM_BYPASS_FED, 100, 100);   //Deadtime of 10us
            }
            hall_sensor_previous = hall_sensor_value;
        }else{
            printf("FRENADO!\n");
            mcpwm_config_t pwm_config;
            pwm_config.frequency = 1000;    //frequency = 1000Hz
            pwm_config.cmpr_a = 0.0;    //duty cycle of PWMxA = 50.0%
            pwm_config.cmpr_b = 0.0;    //duty cycle of PWMxb = 50.0%
            pwm_config.counter_mode = MCPWM_UP_COUNTER;
            pwm_config.duty_mode = MCPWM_DUTY_MODE_0;
            mcpwm_init(MCPWM_UNIT_0, MCPWM_TIMER_0, &pwm_config);    //Configure PWM0A & PWM0B with above settings
            mcpwm_init(MCPWM_UNIT_0, MCPWM_TIMER_1, &pwm_config);    //Configure PWM1A & PWM1B with above settings
            mcpwm_init(MCPWM_UNIT_0, MCPWM_TIMER_2, &pwm_config);    //Configure PWM2A & PWM2B with above settings
        }
        vTaskDelay(pdMS_TO_TICKS(10));
    
    }
}
// Functions for ADC
static void check_efuse(void)
{
#if CONFIG_IDF_TARGET_ESP32
    //Check if TP is burned into eFuse
    if (esp_adc_cal_check_efuse(ESP_ADC_CAL_VAL_EFUSE_TP) == ESP_OK) {
        printf("eFuse Two Point: Supported\n");
    } else {
        printf("eFuse Two Point: NOT supported\n");
    }
    //Check Vref is burned into eFuse
    if (esp_adc_cal_check_efuse(ESP_ADC_CAL_VAL_EFUSE_VREF) == ESP_OK) {
        printf("eFuse Vref: Supported\n");
    } else {
        printf("eFuse Vref: NOT supported\n");
    }
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
void app_main(void)
{
    //SETUP MCPWM
    printf("Testing MCPWM...\n");
#if CHANGE_DUTY_CONTINUOUSLY
    xTaskCreate(change_duty, "change_duty", 2048, NULL, 2, NULL);
#endif
    cap_queue = xQueueCreate(1, sizeof(capture)); //comment if you don't want to use capture module
    cap_queue2 = xQueueCreate(1, sizeof(uint32_t)); //comment if you don't want to use capture module
#if GPIO_HALL_TEST_SIGNAL
    xTaskCreate(gpio_test_signal, "gpio_test_signal", 2048, NULL, 2, NULL);
#endif
    if(cap_queue == NULL || cap_queue2 == NULL){
        printf("Error creating the cap_queue or cap_queue2");
    }
    xTaskCreate(disp_captured_signal, "mcpwm_config", 4096, NULL, 5, NULL);  //comment if you don't want to use capture module
    xTaskCreate(setup_print_ADC, "setup_print_ADC", 4096, NULL, 5, NULL);  //comment if you don't want to use capture module 
    // @TODO fix with que
    xTaskCreate(mcpwm_example_bldc_control, "mcpwm_example_bldc_control", 4096, NULL, 5, NULL);
}

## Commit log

2021-04-19 ESP example BLDC motor control
2021-04-19 Version con ADC, se resetea el micro
    [mcpwm_bldc_control_hall_sensor_example.c]
2021-04-19 Finally motor works only by printing each condition
2021-04-20 Added the schematic and PCB design, PCB version V0.3
    [controller_bldc.kicad_pcb, controller_bldc.sch]
2021-04-20 PCB v0.5 after autoroute
    [controller_bldc.dsn, controller_bldc.kicad_pcb]
2021-04-20 Fix in the IR2103 group arrangements inside the PCB
    [controller_bldc.kicad_pcb]
2021-04-21 PCB in v0.7, only relay to change for next and maybe the first tri
    [controller_bldc.dsn, controller_bldc.kicad_pcb, controller_bldc.sch]
2021-04-21 Fix kicad_pcb
    [controller_bldc.dsn, controller_bldc.kicad_pcb]
2021-04-21 V0.8 with everything except for the relay that should consume less current, 36V-Power is fixed.
    [controller_bldc.kicad_pcb, controller_bldc.sch]
2021-04-21 Fix kicad_pcb because of bad merge solve
    [controller_bldc.dsn, controller_bldc.kicad_pcb]
2021-04-21 Fixed the schematic for the three 220uF capacitors and the connections Connections of MCPWM GPIOs inside the main/*.c were changed to correspond with the schematic
    [controller_bldc.sch]
2021-04-21 This is with previous tracks, so 2mm are kept but narrowers are deleted. Version before autorouting
    [controller_bldc.dsn, controller_bldc.kicad_pcb]
2021-04-21 Deleted unblocked routes to be processed by FreeRouting
    [controller_bldc.kicad_pcb]
2021-04-21 PCB v0.9 after Freerouting, only remaining the verification of the relay. Remember connectors, the fuse and the code for the screen, sensors, current control and also the design and manufacture of th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
    [controller_bldc.dsn, controller_bldc.kicad_pcb]
2021-04-21 Current sensor added in main/mcpwm...example.c
2021-04-22 The second ADC channel is assigned for the current sensor in main/mcpwm...example.c
2021-04-22 Se cambia el nombre del proyecto
2021-04-24 Firmware: project name and val:pwm_config_frequency fixed
2021-04-24 PCB: Added Amp Op library and changed V & A Sensors
    [controller_bldc.sch]
2021-04-27 PCB: Finished with DC Power Sources and Amp. Op. for sensors
    [controller_bldc.sch]
2021-04-27 PCB: Footprints changed for DC Sources and the OPC realy
    [controller_bldc.sch]
2021-04-27 This fixes PCB and Schematic, closes #5, closes #6, closes #7, closes #8
    [controller_bldc.dsn, controller_bldc.kicad_pcb, controller_bldc.sch]
2021-04-28 PCB Finished, this is version 2.0. Closes #9 and closes #10.
    [controller_bldc.dsn, controller_bldc.kicad_pcb, controller_bldc.sch]
2021-04-29 Firmware: All sensors working just fine
2021-04-29 Firmware moved to the FIRMWARE folder NextionTest folder added
    [controller_bldc.dsn, controller_bldc.kicad_pcb, controller_bldc.sch]
2021-04-29 PCB v1.1 with the res. for throttle
    [controller_bldc-B_Adhes.gbr, controller_bldc-B_Cu.gbr, controller_bldc-B_Fab.gbr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]
2021-04-29 To be reviewed by Yahico PCB
    [controller_bldc-B_Adhes.gbr, controller_bldc-B_Cu.gbr, controller_bldc-B_Fab.gbr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]
2021-04-29 Before freerouting
    [controller_bldc.dsn, controller_bldc.kicad_pcb]
2021-04-29 Sento to Yahiko
    [controller_bldc-B_Adhes.gbr, controller_bldc-B_Cu.gbr, controller_bldc-B_Fab.gbr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]
2021-04-30 PCB and FIRMWARE changed, see some failures found. Closes #12, closes #13. Tareas realizadas: 0. Corregir afectación de sobrevoltaje en acelerador 1. Mover motor
    Fallas encontradas:
    Desconectando la PCB china disminuye la corriente consumida y funcionan independientes los sensores, sin que V_Sensor altere a los otros sensores.
    Error en acelerador, voltaje de salida del acelerador sin oprimir: 3.2V
    Voltaje de regulación en la segunda fuente de 18V -> Concetar resistencia de consumo en la salida de 100 ohms
2021-04-30 README updated with DC-DC converter's datasheet Closes #11
    [controller_bldc.sch]
2021-05-01 PCB working, printing sensors in a good-looking console Fixed the issue with multiple sensors affected when overvoltage in throttle. Closes #16, closes #17, closes #18
    [controller_bldc.sch]
2021-05-02 Fixing incluiding everything except for TODO and Build Folders
    [controller_bldc-B_Adhes.gbr, controller_bldc-B_Cu.gbr, controller_bldc-B_Fab.gbr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]
2021-05-02 After refreshing repo, only includes src, PCB. All Build folders are excluded
    [controller_bldc-B_Adhes.gbr, controller_bldc-B_Cu.gbr, controller_bldc-B_Fab.gbr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]
2021-05-10 PCB v1.1 printed with some errors.
    [controller_bldc-B_Adhes.gbr, controller_bldc-B_Cu.gbr, controller_bldc-B_Fab.gbr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]
2021-05-10 Firmware working with Nextion and Sharky sensors. TODO - Check current sensor with motor. TODO - Check battery sensor with motor. TODO - Calculate and display speed. TODO - Calculate and display dist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
2021-05-11 Motor working. Fixed priorities in FreeRTOS tasks.
2021-05-21 Changing all the schematics
    [controller_bldc.sch, electeam.sch]
2021-05-25 Just before separating folders and branches According to version independence
    [controller_bldc.kicad_pcb, controller_bldc.sch, electeam.sch]
2021-05-25 Changed folders to 'Diagramas y Esquemas'
    [electeam.sch]
2021-05-25 Finalmente se separa la electrónica del firmware
    [controller_bldc-B_Adhes.gbr, controller_bldc-B_Cu.gbr, controller_bldc-B_Fab.gbr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]
2021-05-25 Primer avance del esquema global
    [controller_bldc-B_Adhes.gbr, controller_bldc-B_Cu.gbr, controller_bldc-B_Fab.gbr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]
2021-05-25 Ready to create dev/hotfix branches
    [electeam.sch]
2021-05-25 Pending if fan is added or not
    [controller_bldc.sch, electeam.sch]
2021-06-12 Hardware 1.1 working and started with soft+firm-ware Checking and looking for changes to be done inside firmware 1.1. Fan issue still pending.
